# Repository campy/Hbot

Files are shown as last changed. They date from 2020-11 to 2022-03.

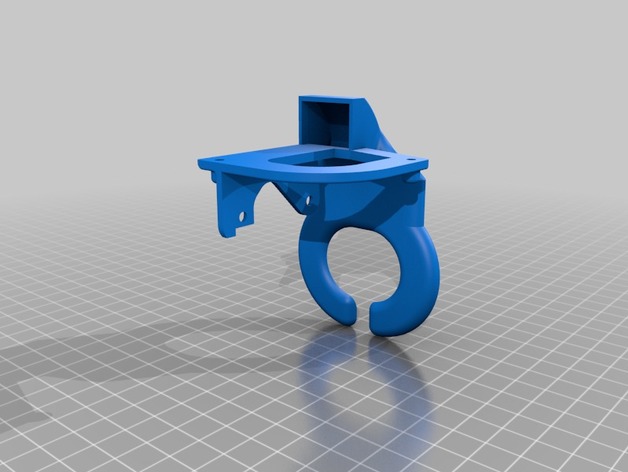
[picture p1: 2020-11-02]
Hbot XL/Source/Titan Aero Full/Blower titan/images/036bd3c3c1cbe7b02644d6485af83f34_preview_featured.jpg

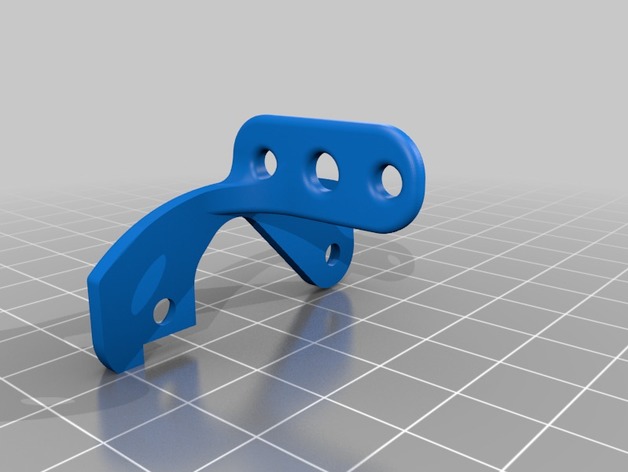
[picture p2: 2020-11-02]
Hbot ST/Source/Titan Aero Full/Blower titan/images/825169e0491ec67ebed7de5d310a97ef_preview_featured.jpg

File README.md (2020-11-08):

# Impresoras 3D Serie Hbot Pro ST / XL

## Licencia
Proyecto Open-Source con licencia CC BY-NC (No comercial)

Usted puede Compartir — copiar y redistribuir el material en cualquier medio o formato

Usted puede Adaptar — remezclar, transformar y construir a partir del material

NoComercial — Usted no puede hacer uso del material con propósitos comerciales

Atribución — Usted debe dar crédito de manera adecuada, brindar un enlace a la licencia, e indicar si se han realizado cambios. Puede hacerlo en cualquier forma razonable, pero no de forma tal que sugiera que usted o su uso tienen el apoyo de la licenciante.





##  Introducción
Diseñada desde cero por [3DCampy](https://blog.3despana.com/sobre-mi/) 

Nuestra impresora está pensada para clientes o empresas que no disponen de tiempo o simplemente no quieren ensamblar montar y calibrar su impresora 3D, por esto nosotros hacemos todo por ti

La impresora se envía completamente ensamblada, calibrada y testada, solo tendrás que sacarla de la caja y empezar a imprimir

Os presentamos la nueva impresora Diseñada y fabricada por 3DCampy / 3DEspana, mas de dos años de desarrollo y miles de horas de impresión han dado sus frutos, con una cinemática de una sola correa Hbot (CoreXY) facilita el mantenimiento y permite movimientos rápidos, precisos y además reduce la masa suspendida en mas de un 25% respecto a otros tipos de cinemáticas aportando mayor calidad de impresión a velocidades mas altas sin la aparición de defectos como Ghosting o ringing

*Montamos cada impresora expresamente para cada cliente con lo cual el plazo de entrega puede variar en función de la carga de trabajo o especificaciones de la maquina

*El tiempo medio de entrega es de 10-15 Días dependiendo del volumen de trabajo, llámanos si necesitas saber exactamente la fecha de entrega

Diseñada para un uso profesional y funcionamiento 24/7 ideal para granjas de impresión o producciones grandes de piezas. Gracias a la gestión wifi podemos enviar los archivos a través de la red, sin tener que usar tarjetas SD y directamente desde el Slicer.

Preparada para impresión de materiales técnicos con cámara caliente, El ABS, ASA, Nylon, PC, Flexibles ya no serán un problema, el modelo panelado de Hbot Pro dispone de una cámara caliente pasiva que es capaz de mantener entre 55º-60º la temperatura ambiente interior, gracias a la cámara caliente podremos imprimir materiales técnicos con acabados inmejorables, sin warping y sin cracking por lo que obtendremos piezas de calidad, solidas y resistentes hasta con los materiales mas complejos

Chasis de aluminio Nuestra Hbot está fabricada con un chasis de aluminio de 5mm lo que aporta una rigidez estructural impresionante, ademas los perfiles son de 40mm esto evita pandeos y torsiones en la estructura imprimiendo a velocidades altas

¿Por que hemos elegido un extrusor basado en titan aero? Aunque en el mercado hay un montón de extrusores hemos elegido para nuestra impresora un extrusor basado en titan aero, eso nos permite tener un extrusor, compacto ligero, con mucha fuerza de tracción y los mas importante es el extrusor mas estándar y utilizado en la impresión 3D, estos nos aporta compatibilidad con barrels y puntas de V6 (Los barrels mas comunes en la industria) y de los cuales hay multitud de opciones (All metal, con PTFE, Bi-Metal, titanio etc..) Por lo que podremos adaptar rápidamente nuestra maquina a cualquier material o novedad del mercado y además podremos conseguir repuestos económicos y rápidos de conseguir 

Proyecto Open Source Como todas nuestras impresoras, publicamos todos los componentes, diseños y piezas impresas, esto quiere decir que podrás reparar o imprimir cualquier componente con solo entrar en el repositorio y beneficiarte de las mejoras, mods, o campañas de forma gratuita

En constante evolución A medida que vamos fabricando mas unidades de nuestras impresoras Hbot, vamos puliendo el propio diseño es decir tu impresora no se quedará obsoleta y será compatible con las futuras mejoras propuestas en el proyecto

Fiabilidad y fácil mantenimiento La impresora Hbot Pro lleva guias de precisión MGN12 esto nos permite prácticamente olvidarnos del manteamiento y holguras, nos garantiza podemos imprimir miles de horas sin tener que realizar reparaciones o ajustes. Toda la parte mecánica de la impresora se sitúa en la parte superior esto nos facilita el mantenimiento, reparación o desatasco de la impresora ya que al quitar la tapa toda la mecánica quedará vista y de fácil acceso

Características Técnicas:

Estructura:

Chasis en aluminio de 5mm

Refuerzos de 40mm

Panelado en aluminio pintado al polvo

Dimensiones de impresión útiles:

Eje X – 325mm

Eje Y – 325mm

Eje Z – 400mm

Dimensiones exteriores

Panelada: Ancho 550mm Alto 630mm / Profundidad 630mm

Sin Panelar Ancho 550mm / Alto 590mm / Profundidad 630mm

Cinemática:

Cinemática Hbot (CoreXY) con una sola correa

Poleas de precisión con tornillos mecanizados

Correa anti-friccion Powergrip

Motores Nema17 con husillo de precisión en el eje Z

Tuercas POM anti-backlash para el eje Z

Guiás de precisión mecanizadas MGN12

Rodamientos lineales de re-circulacion de bolas MSC

Varillas de acero cromado rectificadas

Electrónica:

Electrónica de 32 Bits basada en Duet 3D con Reprap firmware

Alimentación a 24V

Sensor de autonivel Inductivo

Mapa de nivelado de la base caliente con macro

Conexión Wifi de 2,4Ghz

Panel web de control de impresión

Posibilidad de enviar las piezas por red desde el slicer

Monitorización de la impresión a través del panel web

Personalización y automatizacion a través de macros

Drivers TMC 2660 Silenciosos

Pantalla de 5” táctil

Extrusión:

Extrusor compatible con E3D Titan Aero

Filamento

Boquilla de 0,4mm

Barrel-Esparrago bi-metal (Compatible con muchos materiales)

Desmultiplicación 1/3 para mayor par de empuje

Extrusión directa completamente guiada compatible con filamentos flexibles

Funda de silicona para proteger los goteos y estabilizar la temperatura del bloque

Base de impresión:

Sensor inductivo de autonivel

Fleje flexible para la correcta extracción de la bandeja de impresión

Lamina anti-warping ya instalada

Compatible con laminas PEI o flejes texturizados

Alimentación y base caliente:

Fuente de alimentación 24V 20A

Conector trasero C14 con fusible interior

Conector Mini USB en el panel trasero

Base caliente a 24V (Temperatura máxima 110º-120º)

## Compatibilidades
- Compatible con extrusor Titan Aero
- Compatible con electronica Duet 3D

## Información de cambios y mejoras
[Ir a Wiki](https://wiki.3despana.com/index.php?title=Hbot_pro)

## Donde comprar los materiales o impresora completa
[3DEspana.com](https://3despana.com)

## Videos
Presentación
[Youtube] (https://youtu.be/CTP1-fysIOw)

Presentacion Hbot XL 
[Youtube] (https://youtu.be/yqlnOjQYD-E)

## Videos Manuales tutoriales
Manual de como calibrar el OFFSET
[Youtube] (https://youtu.be/fizcIWx3F3U)

Manual Desmontar extrusor
[Youtube] (https://youtu.be/Jr3bt5Bu2t4)

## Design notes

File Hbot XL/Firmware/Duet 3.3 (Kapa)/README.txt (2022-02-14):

Recursos
FW - 3.3 : https://github.com/Duet3D/RepRapFirmware/releases/download/3.3/Duet2CombinedFirmware.bin
DWC - 3.3 :https://github.com/Duet3D/RepRapFirmware/releases/download/3.3/DuetWebControl-SD.zip
PannelDue - 3.3
WifiServer - 1.26 : https://github.com/Duet3D/RepRapFirmware/releases/download/3.3/DuetWiFiServer.bin

Configuracion Parametrizada:
en \sys\config-var.g

Para seccionar nuestro tipo de maquina o sensor Z editamos config.g
; ==============================================================
;
; Hbot XL by Campy3d
;
global model = 2		; 1 = XL 		2 = ST    for  CUSTOM (edit in config-var.g on you model type XT or ST)
global probetype = 2		; 1 = IR mini	2 = Superpinda
; ===============================================================

Pendiente:
Medidas del husillo para HBOT ST

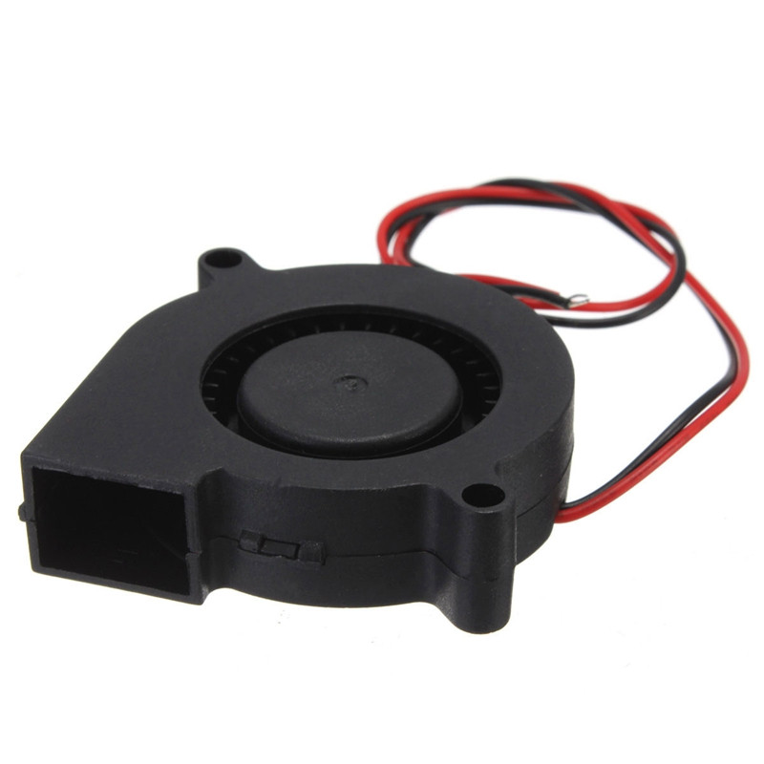
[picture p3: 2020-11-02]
Hbot XL/Source/Titan Aero Full/Radial Cooling Fan 50mm DC12V/Double-50-x-50-x-15mm-12V-DC-50mm-Blow-Radial-Cooling-Fan-for-Electronic-3D.jpg

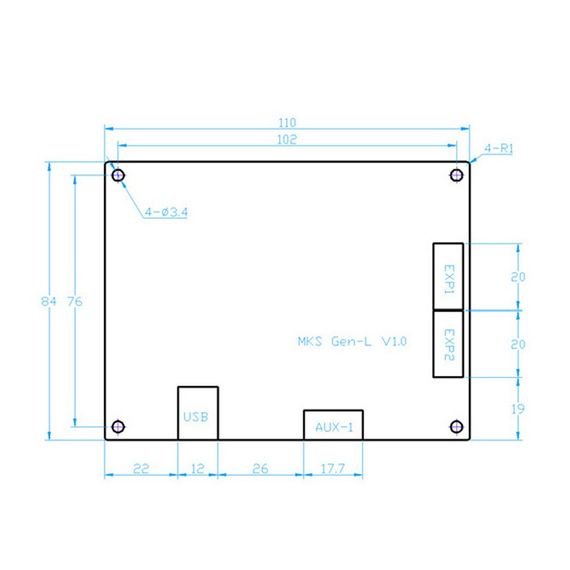
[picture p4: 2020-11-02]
Hbot ST/Source/Electronic/MKS Gen L/Gen L.jpg

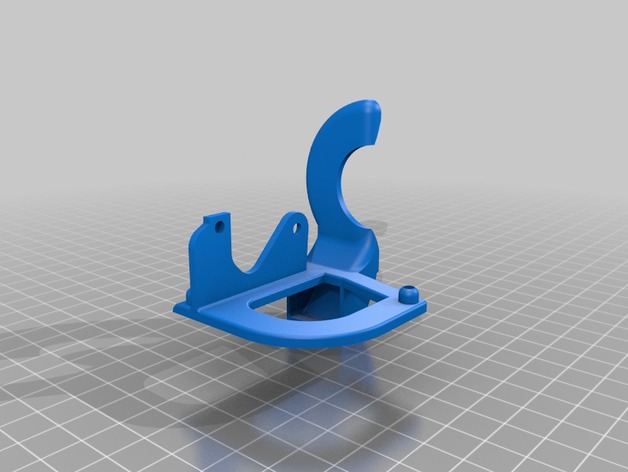
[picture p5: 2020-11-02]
Hbot ST/Source/Titan Aero Full/Blower titan/images/ec55eea4d29ecc0d4c0dcb4f45196d15_preview_featured.jpg

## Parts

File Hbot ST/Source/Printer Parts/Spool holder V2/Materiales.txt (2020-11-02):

2 x tuercas m8 autoblocantes
1 x varilla roscada m8 180mm
2 x rodamientos 608zz

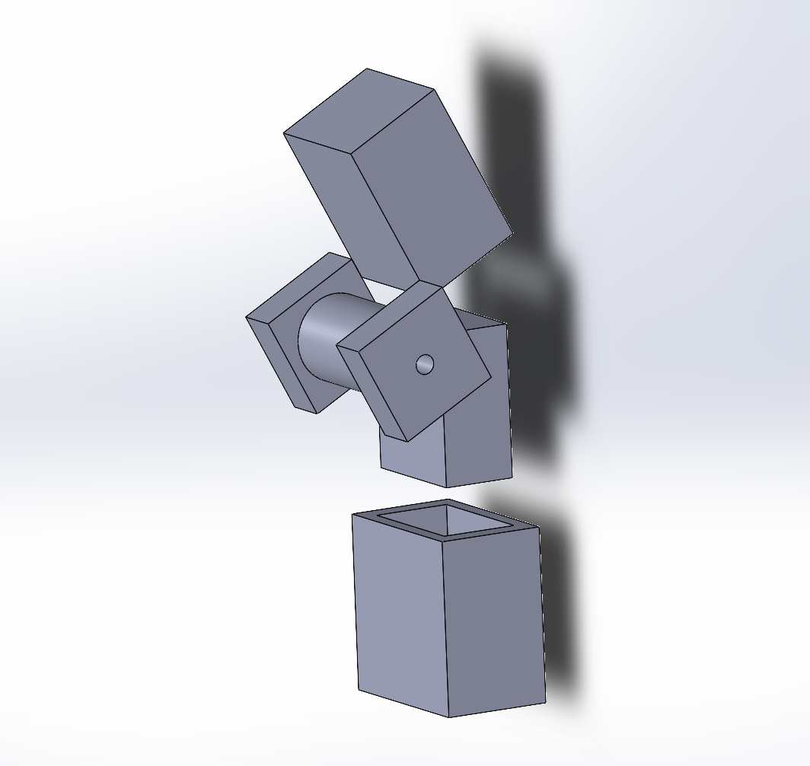
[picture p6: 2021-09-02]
Hbot XL/Source/Printer Parts/Bisagra/inicio.png

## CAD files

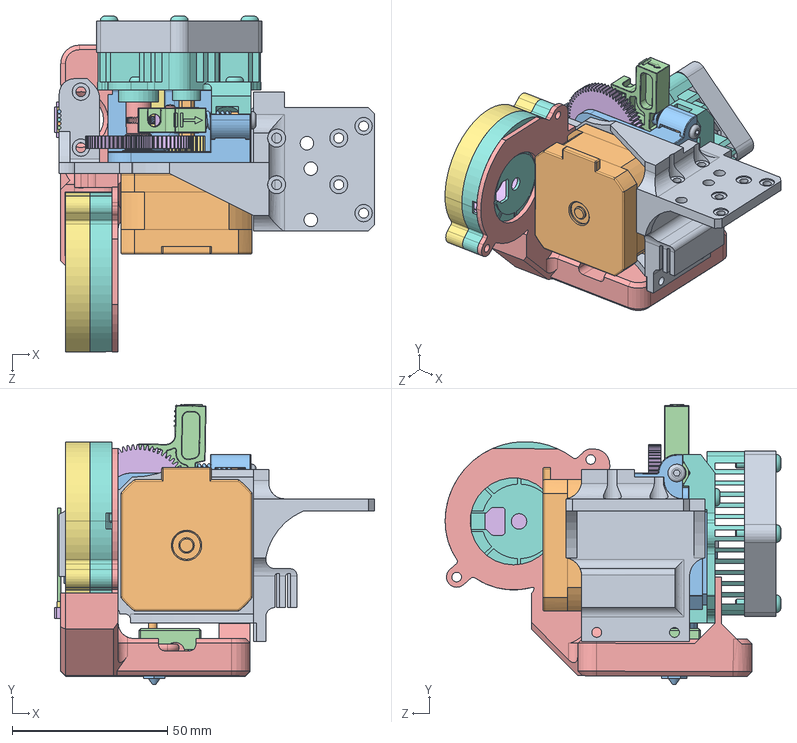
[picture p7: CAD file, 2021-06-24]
Hbot XL/Bltouch MOD/EnsamblajeEX-BLT.SLDASM
103.0 x 90.2 x 108.1 mm
Sop EX-XL-BLT
Nema 17
Base
9x5x3mm bearing x 2
hobbed wheel
filament gear
motor gear
cover
m3x8
M3 nut
idler spring
tensioner
idler bearing pin
idler bearing
guide tube
ISO 7380 - M3 x 28 v1 x 8
Fan 40 X 40 X 10 v4
E3D v6 HotEnd - Heatbreak
E3D v6 HotEnd - Nozzle
E3D v6 HotEnd - Heat Block
Ceramic Cartridge Heater
Thermistor
HEXAGON SOCKET HEAD CAP SCREWS_SCB3-4
HEXAGON SOCKET HEAD CAP SCREWS_SCB3-10
Flat Washers_PWF3
93245A111.step
BL-touch.step
BL-touch-0.step
BL-touch-1.step
BL-touch-2.step
BL-touch-3.step
BL-touch-4.step
BL-touch-5.step
BL-touch-6.step
BL-touch-7.step
BL-touch-8.step
LayerFan-Bltouch
turbine
top
bottom

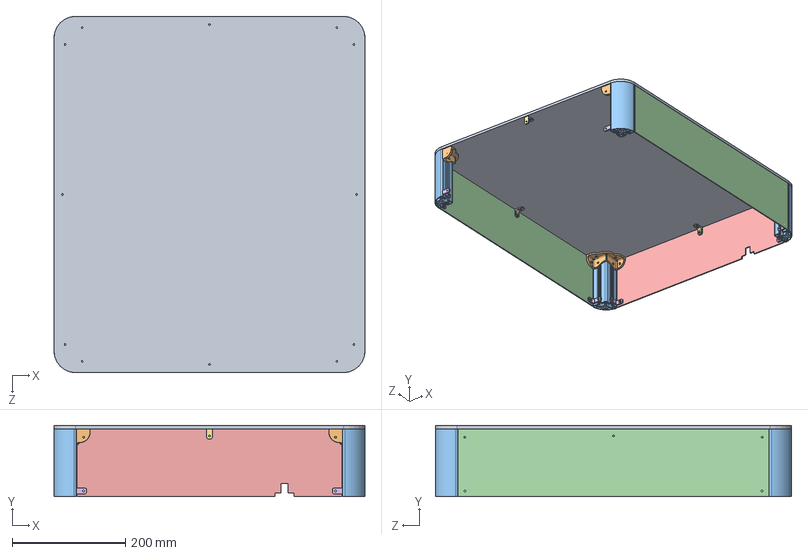
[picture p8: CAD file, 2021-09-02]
Hbot XL/Cover Panels/Tapa XL.SLDASM
550.0 x 126.0 x 630.0 mm
Cover panel topXL
Square V2 x 4
Perfil 40 Short x 4
UP Panel XL LR X2 x 2
UP Panel XL Back
Sop Up Panel x 8
Sop Up XLRef x 4

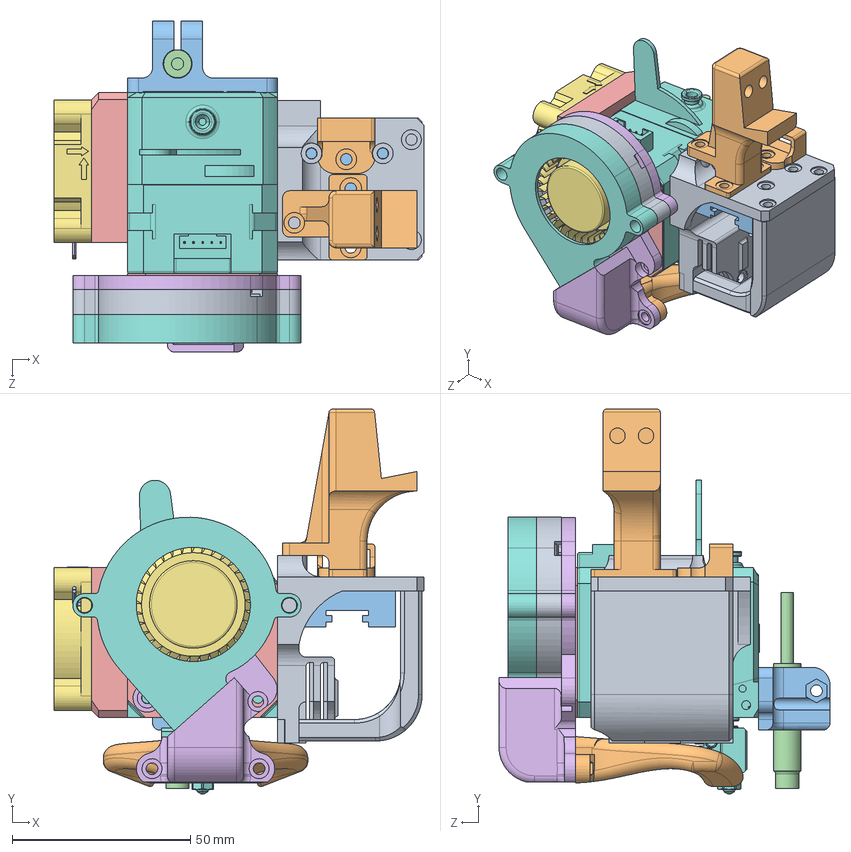
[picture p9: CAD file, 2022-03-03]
Hbot XL/LGX Extruder/Ensamblaje-LGX.SLDASM
103.6 x 107.8 x 92.8 mm
Sop EX-XL-LGX
Sop Cadeneta 15 NF
LGX-FF-RH-heatsink1.STEP
LGX-FF-RH-heatsink2.STEP
LGX-FF-RH-heatsink3.STEP
LGX-FF-RH-heatsink4.STEP
LGX-FF-RH-heatsink5.STEP
LGX-FF-RH-heatsink6.STEP
Refuerzo-Pinda
Sop EndY
Super-Pinda-LGX
Super pinda
Pantilla nema
Soporte-Fan-5015
turbine
top
bottom
Duct v2.1 Straight V6.step
MGN12C

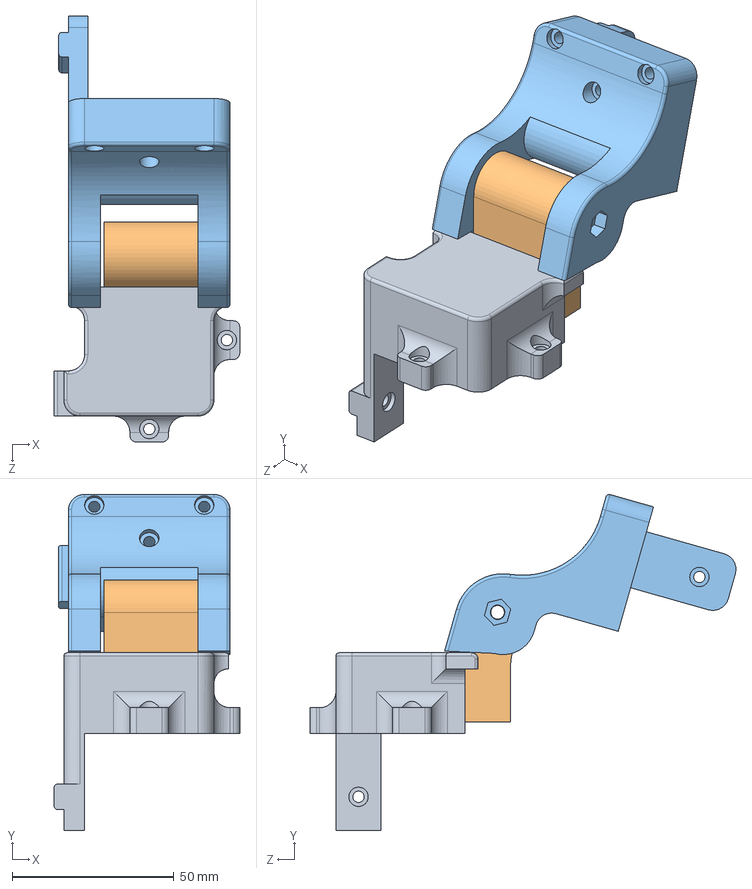
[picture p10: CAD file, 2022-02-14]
Hbot XL/Source/Printer Parts/Bisagra/Ensam-bisagra.SLDASM
57.4 x 103.9 x 131.7 mm
Inferior
perno
superior

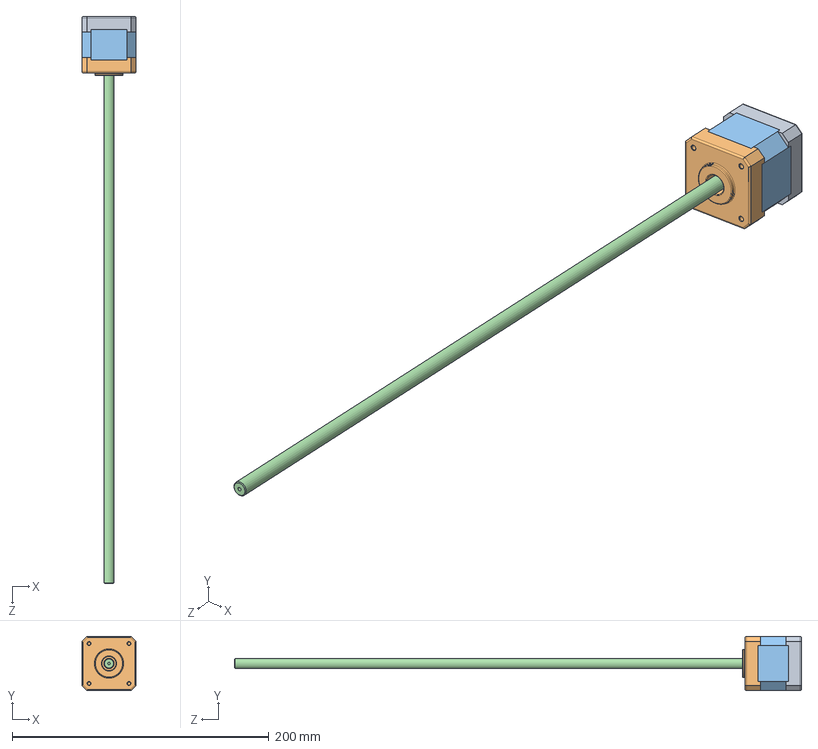
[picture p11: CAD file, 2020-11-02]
Hbot ST/Source/Nema Z/Stepper motor/Nema Z3.SLDASM
42.3 x 42.3 x 441.5 mm

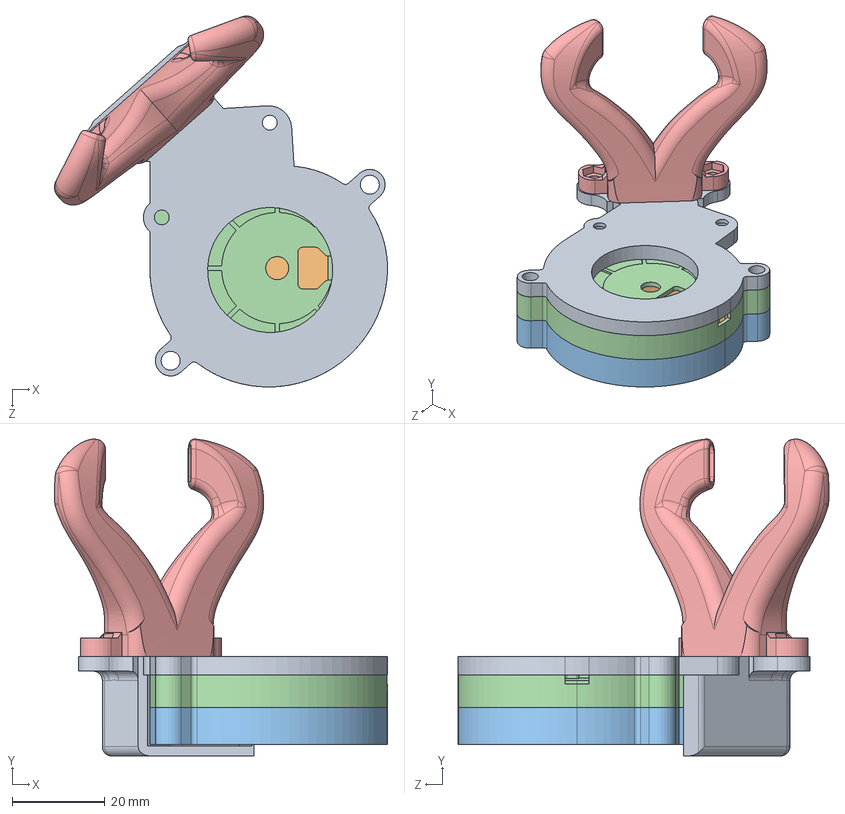
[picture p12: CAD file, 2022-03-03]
Hbot XL/LGX Extruder/Ensamblaje-Layerfan.SLDASM
71.9 x 68.4 x 80.1 mm
Soporte-Fan-5015
turbine
top
bottom
Duct v2.1 Straight V6.step

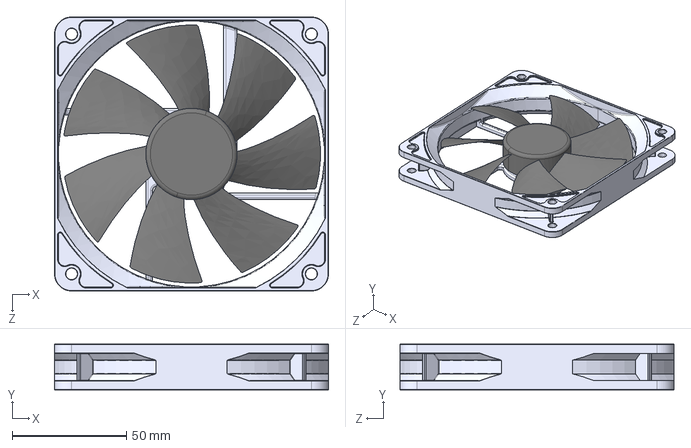
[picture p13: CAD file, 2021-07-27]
Hbot XL/Source/Fan 120mm/Fan_Assembly.STEP
120.0 x 20.0 x 120.0 mm
Fan_Case
Fan

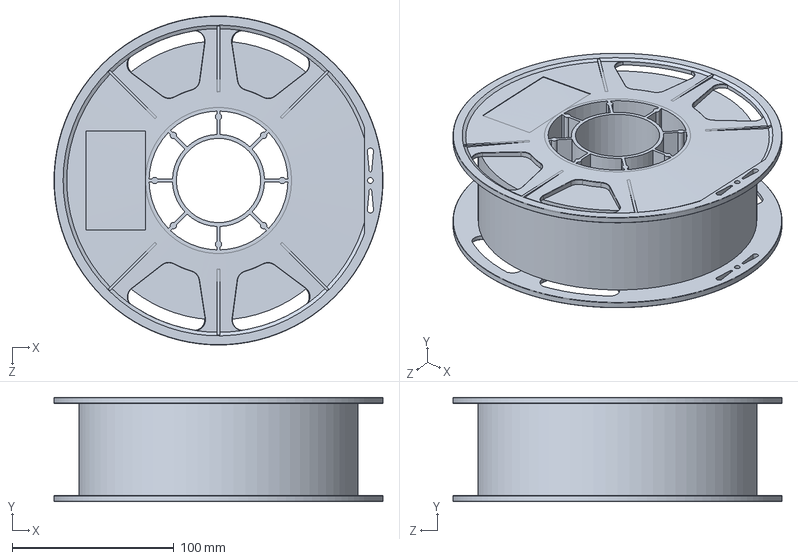
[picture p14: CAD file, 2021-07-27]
Hbot XL/Source/Filament Spool/Filament Spool Blue.step.SLDASM
203.2 x 64.4 x 203.2 mm

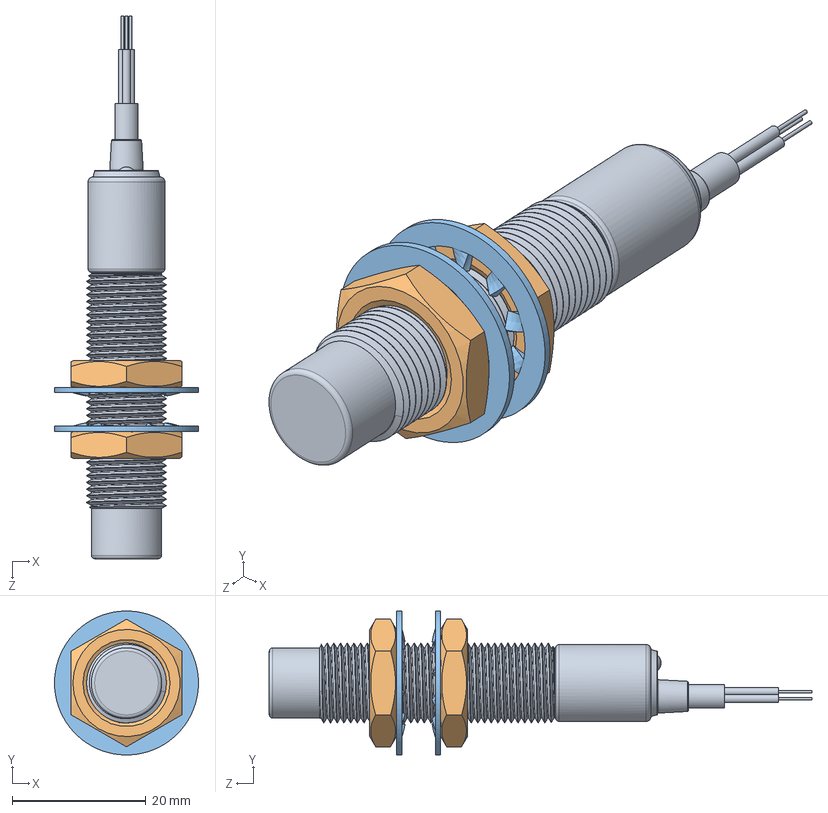
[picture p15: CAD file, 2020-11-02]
Hbot XL/Source/Inductive Sensor/LJ12A3-4-Z.SLDASM
21.5 x 21.5 x 81.0 mm
LJ12A3-4-Z
Гайка М12 x 2
Шайба x 2

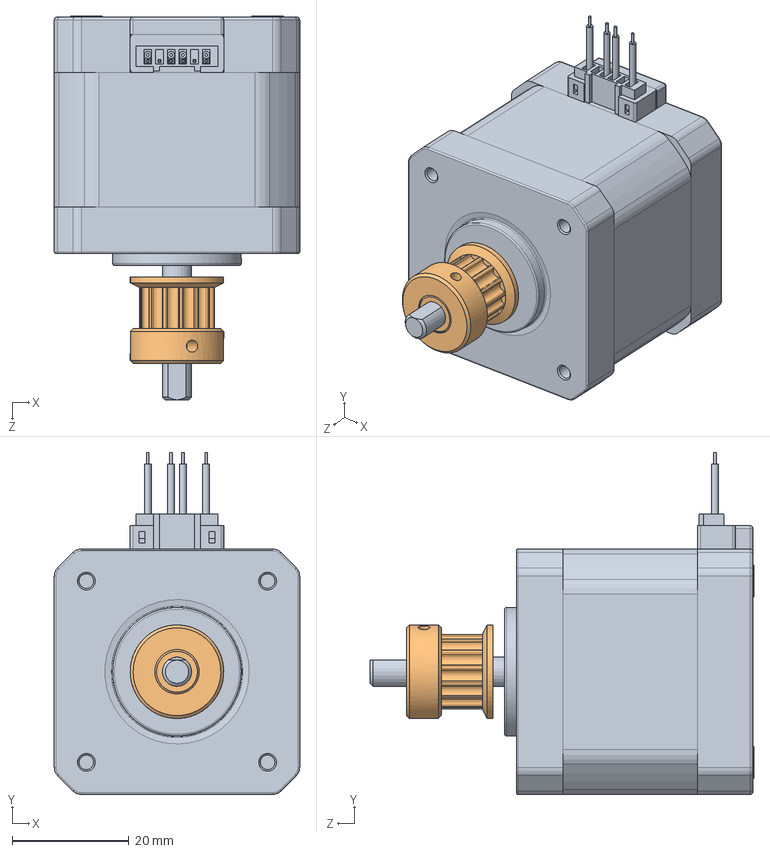
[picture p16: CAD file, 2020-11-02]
Hbot XL/Source/Mot XY/Mot Y.SLDASM
42.0 x 58.5 x 65.7 mm
nema_17_motor
Polea GT2

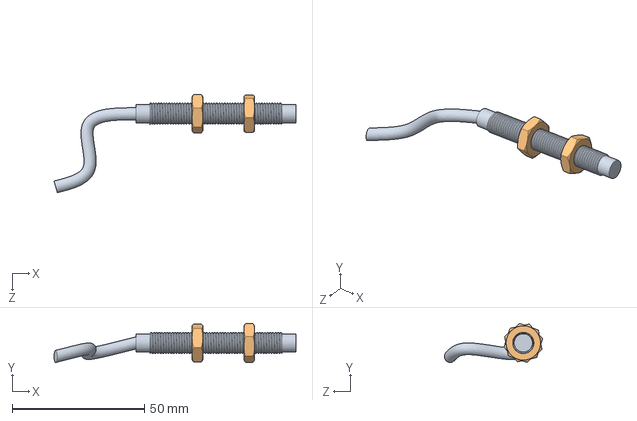
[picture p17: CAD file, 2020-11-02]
Hbot XL/Source/Sensor 8mm/Proximity Sensor M8 size 8 mm NPN NO NC.SLDASM
91.6 x 14.8 x 37.2 mm
Proximity Sensor
hex nut jam_am x 2

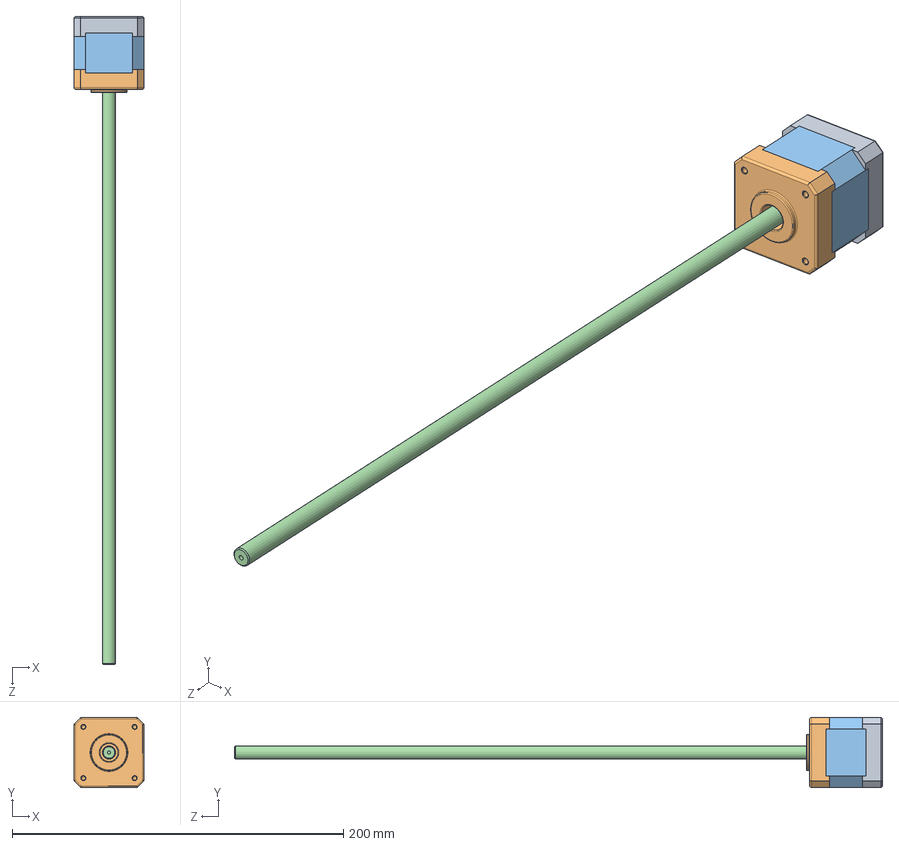
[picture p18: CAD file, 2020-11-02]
Hbot ST/Source/Nema Z/Stepper motor/Stepper motor Assy.SLDASM
42.3 x 42.3 x 391.5 mm

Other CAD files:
Hbot XL/Source/Electronic/Duet Wifi/Molex PCB 3 pin v2 v6_1.sldasm
Hbot XL/Source/Endstop Micro/Component3.sldasm
Hbot ST/Source/Endstop Micro/Component2.sldasm
Hbot XL/Mini led Sensor MOD/Ensamblaje-Miniled.SLDASM
Hbot ST/Cover Panels/Asidero.SLDPRT
Hbot ST/Cover Panels/Asidero.STL
Hbot ST/Cover Panels/Back.DXF
Hbot ST/Cover Panels/Back.SLDPRT
Hbot ST/Cover Panels/Cover panel top.SLDPRT
Hbot ST/Cover Panels/Front.DXF
Hbot ST/Cover Panels/Front.SLDPRT
Hbot ST/Cover Panels/Panel electronica.SLDPRT
Hbot ST/Cover Panels/Perfil 40 Short.SLDPRT
Hbot ST/Cover Panels/Right.DXF
Hbot ST/Cover Panels/Right.SLDPRT
Hbot ST/Cover Panels/Top cover.SLDASM
Hbot ST/Cover Panels/UP Panel X2 F-B-X2.DXF
Hbot ST/Cover Panels/UP Panel X2 F-B.SLDPRT
Hbot ST/Cover Panels/UP Panel X2 LR.DXF
Hbot ST/Cover Panels/UP Panel X2 LR.SLDPRT
Hbot ST/Cover Panels/UP Panel X2 LRFront.DXF
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

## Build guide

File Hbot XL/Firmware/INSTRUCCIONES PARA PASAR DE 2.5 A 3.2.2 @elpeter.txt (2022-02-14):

Peter Chan, [17.06.21 08:45]
[ Archivo : HBot_Update_RRF2_TO_RRF3.zip ]
Actualización de RRF2 a RRF3.2.2 en HBot:

1.- Extraer la SD y hacer una copia de seguridad de su contenido.
2.- Meter el contenido del zip "HBotRRF3.2.2.zip" en la SD, sobreescribir lo que sea necesario.
3.- Meter la SD En la Duet y encender la Hbot.
4.- Conectar al DWC de la HBot e ir a "System", pulsar sobre "Upload System Files" y subir el zip "Duet2and3Firmware-3.0.zip" actualizará a RRF 3
5.- Apagar HBot y sacar SD y meter el "DuetWiFiServer.bin" en la carpeta "sys"
6.- Meter la SD en la duet y encender la HBot. Desde la pantalla, en la consola:
  M552 S0
  M552 S-1
  M997 S1
7.- Reiniciar HBot.
8.- Conectar por DWC e ir a "System", pulsar sobre "Upload System Files" y subir el zip "Duet2and3Firmware-3.2.2.zip" actualizará a RRF 3.2.2
9.- Una vez reiniciada hacer los pasos normales de calibración, mallado, etc etc...
10. - DISFRUTAR!!!

Peter Chan, [17.06.21 08:45]
Buenos días!! He quitado los .bin del HBotRRF3.2.2.zip porque sino se iba a liar...

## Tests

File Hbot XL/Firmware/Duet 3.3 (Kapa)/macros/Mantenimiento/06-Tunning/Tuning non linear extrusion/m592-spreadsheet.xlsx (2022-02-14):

mm asked for = | 100 |  | Steps/mm = | 6640
mm/s | Extruded | 1st Added % | 2nd Added % | 3rd Added % | 4th Added % | 5th Added % | 6th Added % | Sum %
1 | 101.5 | -0.01477832512 | 0.0002183988934 | 4.769807666e-08 | 2.275106517e-15 | 5.176109663e-30 | 2.679211125e-59 | -0.01455987853
2 | 100 | 0 | 0 | 0 | 0 | 0 | 0 | 0
3 | 98.5 | 0.0152284264 | 0.0002319049705 | 5.377991534e-08 | 2.892279294e-15 | 8.365279515e-30 | 6.997790136e-59 | 0.01546038515
4 | 93.5 | 0.06951871658 | 0.004832851955 | 2.335645801e-05 | 5.45524131e-10 | 2.975965775e-19 | 8.856372294e-38 | 0.07437492554
5 | 91.5 | 0.09289617486 | 0.008629699304 | 7.447171008e-05 | 5.546035603e-09 | 3.07585109e-17 | 9.46085993e-34 | 0.1016003514
 |  |  |  |  |  | mm/s | Extruded | Dev From Ave
 |  |  |  |  |  | 1 | 101.5 | 4.50%
 |  |  |  |  |  | 2 | 100 | 3.00%
 |  |  |  |  |  | 3 | 98.5 | 1.50%
 |  |  |  |  |  | 4 | 93.5 | 3.50%
 |  |  |  |  |  | 5 | 91.5 | 5.50%
 |  |  |  |  |  | Average | 97
 |  |  |  |  |  | Steps Change | 0.97
 |  |  |  |  |  | Steps Result | 6440.8
b (M592 A) = | 0.001190145706
a (M592 B) = | 0.00491323214 |  | M592 D0 A0,0011901457064101 B0,00491323213970553
c (M592 NA) = | -0.02224083394

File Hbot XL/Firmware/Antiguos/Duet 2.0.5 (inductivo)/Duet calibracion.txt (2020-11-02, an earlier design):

PID Hotend M303 H1 S240
PID Cama M303 H0 S70
Luego M500 para guardar o M307 H1 para ver los valores

Sensor de filamento
M591 D0 P2 C3 S1

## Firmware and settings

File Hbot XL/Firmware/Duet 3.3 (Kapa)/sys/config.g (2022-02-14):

; Configuration file for Duet WiFi (firmware version 3)
; executed by the firmware on start-up
; ==============================================================
;
; Hbot XL by Campy3d
; RECUERDA BORRAR EL CONFIG-OVERRIDE.G si cambias el tipo de probe
;
global model = 1								; 1 = XL 		2 = ST    for  CUSTOM (edit in config-var.g on you model type XT or ST)
global probetype = 2                            ; 1 = IR mini    2 = Superpinda    3 = 10mm Inductive
global meshP = 3								; X = size of mesh matrix size: 3 = 3x3 ; 5 = 5x5 ; 7 = 7x7 ; 9 = 9x9; 11 = 11 x 11
;
; OJO con las poleas, revisa si son de 16T o 20T para los pasos de M92		16T = 100 pasos		20T = 80 pasos
; ===============================================================
; Load model type
M98 P"0:/sys/config-var.g" S{global.model} L0 Z0  

; General preferences
G90												; send absolute coordinates...
M83												; ...but relative extruder moves
M550 P"HBot XL RRF3"						    ; set printer name
M669 K1											; select CoreXY mode

; Network

M552 S1											; enable network
M586 P0 S1										; enable HTTP
M586 P1 S1										; enable FTP
M586 P2 S0										; enable Telnet

; Drives
M569 P0 S1										; X physical drive 0 goes forwards
M569 P1 S0										; Y physical drive 1 goes backwards
M569 P2 S1										; Z1 physical drive 2 goes forwards
M569 P3 S0										; E0 physical drive 3 goes backwards
M569 P4 S1										; Z2 physical drive 3 goes backwards
M584 X0 Y1 Z2:4 E3								; set drive mapping
M350 X16 Y16 Z16 E16 I1							; configure microstepping with interpolation
M92 X80.00 Y80.00 Z400.00 E400.00				; set steps per mm
M566 X500.00 Y500.00 Z60.00 E600.00				; set maximum instantaneous speed changes (mm/min)
M566 P1
M203 X18000.00 Y18000.00 Z800.00 E4800.00		; set maximum speeds (mm/min)
M201 X2000.00 Y2000.00 Z400.00 E4000.00			; set accelerations (mm/s^2)
M204 P1200.0 T5000.0                                     ; set print and travel accelerations (mm(s^2)
M566 E400						;300	  ; Set maximum instantaneous speed changes (JERKS) (mm/min) ONLY EXTRUDER
M205 X8 Y8 Z8							; Set maximum instantaneous speed changes (JERKS) (mm/seg) XYZ . USE this for Marlin COMPATIBILITY
M906 X1000 Y1000 Z1000 E560 I30					; set motor currents (mA) and motor idle factor in per cent
M84 S30											; Set idle timeout

; Axis Limits
M208 X0 Y0 Z-1 S1								; set axis minima
M208 X{global.sizeX} Y{global.sizeY} Z400 S0							; set axis maxima

; Definimos Leadscrews para el Z_Tilt
;M671 X{global.posZ1,global.posY} Y{global.posZ2,global.posY} S5
M98 P"0:/sys/config-var.g" S0 L{global.model} Z0				; leadscrews at left (connected to Z) and right (connected to E1) of X axis ---	S Ajustarlo segun sensibilidad del probe			        

		        
; Endstops
M574 X1 S1 P"!xstop"							; configure active-low endstop for low end on X via pin xstop
M574 Y2 S1 P"!ystop"							; configure active-low endstop for high end on Y via pin ystop

; Filament Sensor
M98 P"0:/sys/00-Functions/FilamentsensorStatus"

; Z-Probe IR
M98 P"0:/sys/config-var.g" S0 L0 Z{global.probetype}  ; 

; Heaters BED
M308 S0 P"bedtemp" Y"thermistor" T100000 B3950 A"Heated Bed"	; configure sensor 0 as thermistor on pin bedtemp
M950 H0 C"bedheat" T0							; create bed heater output on bedheat and map it to sensor 0
M307 H0 B0 S1.00								; disable bang-bang mode for the bed heater and set PWM limit
M140 H0											; map heated bed to heater 0
M143 H0 S120									; set temperature limit for heater 0 to 120C
M143 H0 P0 S120 A2								; disable temporarily H0 if temp exceeds 120C
M143 H0 P0 S130 A0								; heater fault H0 if temp exceeds 130C
M570 H0 P60 T15 S0 

; Heaters HOTEND
M308 S1 P"e0temp" Y"thermistor" T100000 B4725 C7.06e-8 A"Nozzle T0" ; Configure sensor 1 as thermistor on pin e0temp
M950 H1 C"e0heat" T1									; create nozzle heater output on e0heat and map it to sensor 1
M307 H1 B0 S1.00										; disable bang-bang mode for heater	and set PWM limit
M143 H1 S290											; set temperature limit for heater 1 to 300C
M143 H1 S275 A2											; disable temporarily H1 if temp exceeds 275C
M143 H1 S285 A0											; heater fault H1 if temp exceeds 280C
M570 H1 P10 T30 S0										; heater fault for 10 seg of 30ยบC excursion

;PID backup
M307 H0 R0.322 C632.982:632.982 D5.13 S1.00 V24.3 B0 I0		; Bed PID
M307 H1 R2.813 C295.614:204.933 D6.24 S1.00 V24.5 B0 I0		; Hotend PID

; Fan0 = Part Coooling
M950 F0 C"fan0" Q500							; create fan 0 on pin fan0 and set its frequency
M106 P0 C"LayerFAN" S0 H-1 B0.3					; set fan 0 name and value. Thermostatic control is turned off

; Fan1 = Hotend
M950 F1 C"fan1" Q500							; create fan 1 on pin fan1 and set its frequency
M106 P1 C"ToolFAN" S1 H1 T60					; set fan 1 name and value. Thermostatic control is turned on

; Fan2 = Chamber cam
M950 F2 C"fan2" Q500							; create fan 2 on pin fan2 and set its frequency
M106 P2 I0 C"ChamFAN" S0 H-1                    ; Set fan 2 PWR fan

; Sensor = MotherBoard Cooling
;----MCU & DRIVERS sensors------
;M912 P0 S-13							        ; Cpu temp correction MUST BE ADJUSTED ON EACH BOARD
M308 S3 Y"mcu-temp"	A"MCU"						; create sensor for MCU temp M308 S3 Y"mcutemp"
M308 S4 Y"drivers"	A"Drivers"					; create sensor for drivers temp M308 S4 Y"drivers"

; Tools
M200 D1.75
M563 P0 S"T0" D0 H1 F0							; define tool 0
G10 P0 X0 Y0 Z0									; set tool 0 axis offsets
G10 P0 R0 S0									; set initial tool 0 active and standby temperatures to 0C
M302 S180 R180                                         ; allow extrusion starting from 180°C and retractions already from 180°C

; Firmware Retraction
M404 N1.75										; Define filament diameter for print monitor
M207 S0.95 R0 F2400 Z0							; Firmware retraction

; Bed Compensation Taper
M376 H10										; Bed Compensation Taper 10mm

; Pressure Advance
;M572 D0 S0.09			;PLA
;M572 D0 S0.11			;PETG
;M572 D0 S0.1			;ABS

; LCD
M575 P1 S1 B57600								; enable support for PanelDue

; LEDS
M950 P1 C"e1heat" Q500							;use heater 1 outupt for LED
M42 P1 S1										; turn off LEDS

; Power Management
M911 S23 R24 P"M913 X0 Y0 G91 M83 G1 Z3 E-5 F1000"		; set voltage thresholds and actions to run on power loss
; Select Tool 0
T0												; select first tool
; Load config-override
M501											; load saved parameters from non-volatile memory
; Load Preloaded filamento config
M703
M98 P"0:/macros/04-Maintenance/00-Hbot_DuetVersion"

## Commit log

2020-11-02 Instrucciones + Firmware
    [bed.g, config-override.g, config.g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]
2020-11-02 Upload printers parts
    Printers Parts
    [1mm P5mm.SLDPRT, 1mm P5mm.STL, 2 pole terminal block large v7.sldprt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]
2021-02-22 February Update
    General update with new printer parts
    [Antena-Duet.SLDPRT, Antena-Duet.STL, Front XL.SLDPRT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]
2021-04-08 General Update
    New layer fan V1.1
    New layer fan V2
    New Spool holder
    [1mm P5mm.SLDPRT, 1mm P5mm.STL, 2.5mm P4mm.SLDPRT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]
2021-06-24 June 21 Update
    Add miniled sensor, new frontal frame
    [Asidero.SLDPRT, BackXL.SLDPRT, Cover panel topXL.SLDPRT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]
2021-07-27 July update
    July Update
    [#Fitting_PC4-M6.SLDPRT, 120mm Fan Filter.f3d, 120mm Filter.step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]
2021-09-02 September update
    September General update
    [BackXL.DXF, BackXL.SLDPRT, Ensam-bisagra.SLDASM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]
2022-02-14 First layer update
    First layer update, new ini and profile for prusa slicer
    [start.g]
2022-02-14 General update
    New extruder NF and LGX + Super pinda
    [-0.000mm Less Reprime (OFF).g, -0.025mm Less Reprime.g, -0.050mm Less Reprime.g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]
2022-03-03 General Update
    [Ensamblaje-LGX.SLDASM, Ensamblaje-Layerfan.SLDASM, Soporte-Fan-5015.SLDPRT]
